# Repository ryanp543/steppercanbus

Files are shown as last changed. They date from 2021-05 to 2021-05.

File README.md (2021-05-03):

# CANBus Controlled Stepper Motor Driver 

## Overview

This repository contains the Autodesk Eagle schematic and layout for the custom stepper motor driver developed for the robotic arm mounted on the MIT Bioinstrumentation Lab rover. This information is found in the `Stepper CANBus V2` folder.

The driver had to be able to 1) fit in a CANBus network, 2) require the fewest numbers of wires to operate (in this case, power, ground, and the two CANBus lines), and 3) run on 21 V. What resulted from these constraints is a stepper driver that can be used universally with 24 V bipolar stepper motors and can be easily modified via the interface of the mounted Teensy. Despite the fact that the PCB shape is tailored to this robotic arm, multiple of these drivers can be linked together in any desired daisy chained CANBus network, as long as the last driver in the chain has the switch turned on to activate the 120 Ohm terminator resistor.

The microcontroller chosen for this driver was a Teensy 3.2 based on its widely used interface, easy customization, and relatively small size for a breakout board microcontroller. A Texas Instruments DRV8825 microstepper driver carrier board was selected so it could also be easily mounted onto the custom PCB and take commands from the Teensy. For the step-down power converter, a buck switching regulator (specifically Texas Instruments chip LM2594MX-5.0/NOPBCT-ND) was picked to provide a fixed 500 mA at 5 V, stepped down from an input voltage of around 20 to 24 V. External components such as capacitors and diodes were placed in the external circuit according to the data sheet.

The firmware that is uploaded to the Teensy from the Arduino IDE can be found in the `Stepper_CANBus_Firmware` directory. 

## Contributors

#### Primary Contributors
Ryan Poon from the [MIT Bioinstrumentation Lab](https://bioinstrumentation.mit.edu/) is the primary contributor of this project.

#### Other Contributors
Professor Ian Hunter served as the main advisor.

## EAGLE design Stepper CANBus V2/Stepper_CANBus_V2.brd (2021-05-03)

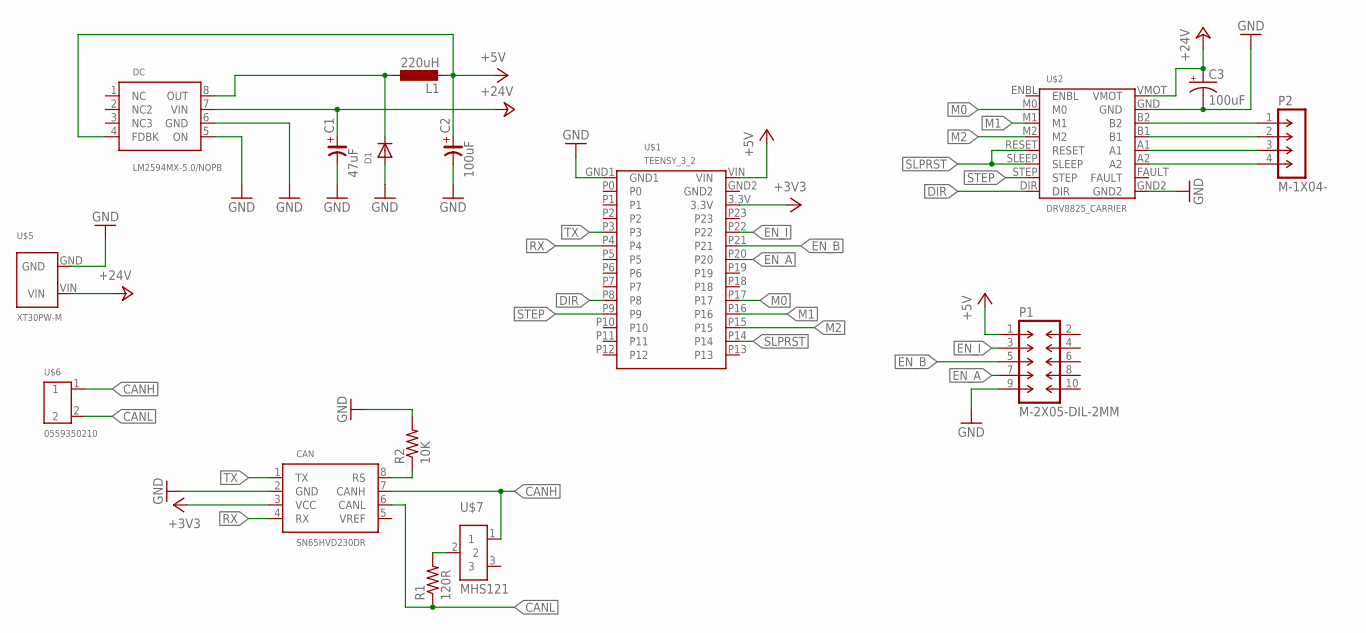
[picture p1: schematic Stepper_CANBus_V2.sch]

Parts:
C1: 47uF; C7343/T
C2: 100uF; C7343/T
C3: 100uF; E2,5-7
CAN: SN65HVD230DR; SOIC8
D1: DIODESOD-323F; SOD-323F
DC: LM2594MX-5.0/NOPB; SOIC8
L1: 220uH; L4532M
P1: M-2X05-DIL-2MM; DIL-2MM-2X05
P2: M-1X04-; DIL-2MM-1X04
R1: 120R; R0603
R2: 10K; R0603
U$1: TEENSY_3_2
U$2: DRV8825_CARRIER
U$5: XT30PW-M
U$6: 0559350210
U$7: MHS121

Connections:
+3V3: CAN.3 (VCC), U$1.3.3V
+5V: C2.+, DC.4 (FDBK), L1.2, P1.1, U$1.VIN
+24V: C1.+, C3.+, DC.7 (VIN), U$2.VMOT, U$5.VIN
CANH: CAN.7 (CANH), U$6.1, U$7.1
CANL: CAN.6 (CANL), R1.1, U$6.2
DIR: U$1.P8, U$2.DIR
EN_A: P1.7, U$1.P20
EN_B: P1.5, U$1.P21
EN_I: P1.3, U$1.P22
GND: C1.-, C2.-, C3.-, CAN.2 (GND), D1.A, DC.5 (ON), DC.6 (GND), P1.9, R2.2, U$1.GND1, U$2.GND, U$2.GND2, U$5.GND
M0: U$1.P17, U$2.M0
M1: U$1.P16, U$2.M1
M2: U$1.P15, U$2.M2
unnamed: CAN.8 (RS), R2.1
unnamed: D1.C, DC.8 (OUT), L1.1
unnamed: P2.1, U$2.B2
unnamed: R1.2, U$7.2
unnamed: P2.2, U$2.B1
unnamed: P2.3, U$2.A1
unnamed: P2.4, U$2.A2
RX: CAN.4 (RX), U$1.P4
SLPRST: U$1.P14, U$2.RESET, U$2.SLEEP
STEP: U$1.P9, U$2.STEP
TX: CAN.1 (TX), U$1.P3

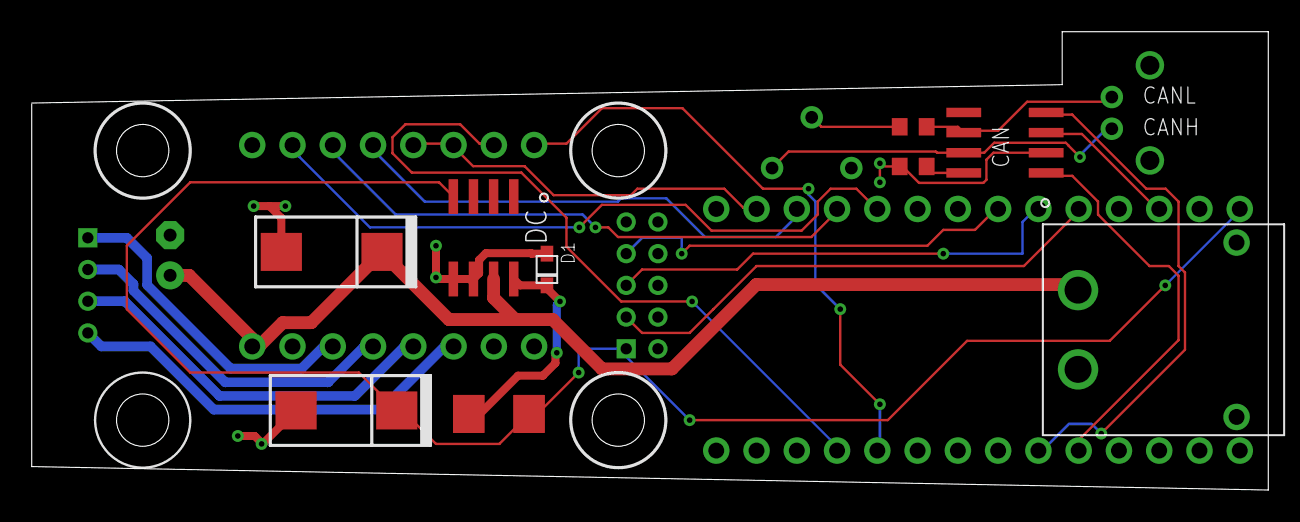
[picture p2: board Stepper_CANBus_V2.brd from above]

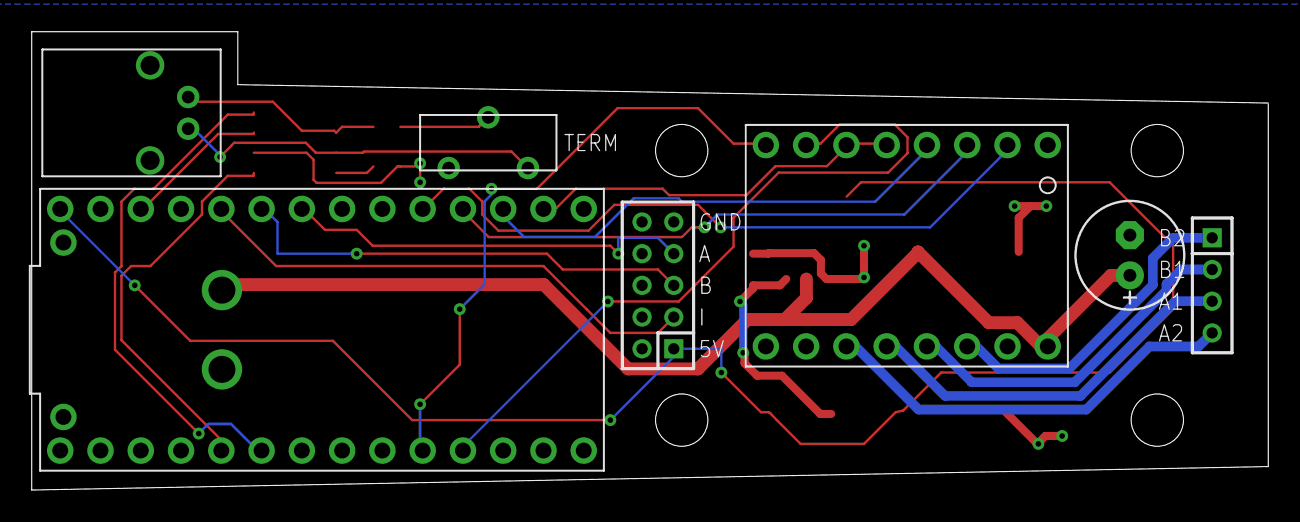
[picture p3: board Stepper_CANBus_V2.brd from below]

Board: 2 copper layers, 78.0 x 28.9 mm, 16 parts (7 on the bottom side), 24 nets.

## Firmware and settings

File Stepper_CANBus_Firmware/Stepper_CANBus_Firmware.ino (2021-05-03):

#include <AccelStepper.h>
#include <FlexCAN.h>

// Stepper constants
const float GEAR_RATIO = 25.2;
const float STEP_RESOLUTION = 200; // 200 steps per revolution
const float CURRENT = 1.5; // 1.5 amps current limit
const int MICROSTEP = 1;

// Encoder constants
const int COUNTS_PER_REV = 2000;
const int ENCODER_TYPE = 2; // X2 encoding

// CANBus ID and command unpacking constants;
const int8_t CAN_ID = 0x4;
const float P_MIN = -25.0f / 6.0f;
const float P_MAX = 25.0f / 6.0f;
const float V_MIN = -45.0f;
const float V_MAX = 45.0f;
const float KP_MIN = 0.0f;
const float KP_MAX = 500.0f;
const float KD_MIN = 0.0f;
const float KD_MAX = 5.0f;
const float T_MIN = -18.0f;
const float T_MAX = 18.0f;
const float I_MIN = -40.0f;
const float I_MAX = 40.0f;

// Initialize LED pin number
const int ledPin = 13;

// Initialize stepper motor pin numbers and variables
const int motorInterfaceType = 1;
const int M0 = 17;
const int M1 = 16;
const int M2 = 15;
const int dirPin = 8;
const int stepPin = 9;
const int sleepReset = 14;
float radPerSecond = 0.0;
volatile float oldPos = 0.0;
AccelStepper stepper = AccelStepper(motorInterfaceType, stepPin, dirPin);

// Initialize encoder pin numbers and variables 
bool atStart = false;
const int encoderA = 20;
const int encoderB = 21;
const int encoderI = 22;
volatile int encoderCount = 0;
volatile float actualPosition = 0.0;

// Initialize exampleClass and reception variable, which are used for CANbus reception. Also initialize transmission message
char reception[8];
char stored[8];
static CAN_message_t txmsg;

class ExampleClass : public CANListener {
public:
   void printFrame(CAN_message_t &frame, int mailbox);
   bool frameHandler(CAN_message_t &frame, int mailbox, uint8_t controller); //overrides the parent version so we can actually do something
};

bool ExampleClass::frameHandler(CAN_message_t &frame, int mailbox, uint8_t controller){
//   Serial.println((String)"ID: " + frame.id);
//   Serial.print("Data: ");
   for (int c = 0; c < frame.len; c++){
      reception[c] = frame.buf[c];
//      Serial.print(reception[c], HEX);
   }
//   Serial.write('\n');

   return true;
}

ExampleClass exampleClass;

void setup() {
  pinMode(ledPin, OUTPUT);

  // Pull sleepReset high
  pinMode(sleepReset, OUTPUT);
  digitalWrite(sleepReset, HIGH);

  // Setup stepper settings
  pinMode(dirPin, OUTPUT);
  pinMode(M0, OUTPUT);
  pinMode(M1, OUTPUT);
  pinMode(M2, OUTPUT);
  stepper.setMaxSpeed(10000);

  // Setup encoder settings
  pinMode(encoderA, INPUT);
  pinMode(encoderB, INPUT);
  pinMode(encoderI, INPUT);
  attachInterrupt(encoderA, doEncoderA, CHANGE);

  // Setup CANBus
  CAN_filter_t filter;
  filter.id = CAN_ID;
  filter.flags.extended = 0;
  filter.flags.remote = 0;
  Can0.begin(1000000);
  Can0.attachObj(&exampleClass);
  
  for (uint8_t filterNum=0; filterNum<8; filterNum++){
    Can0.setMask(0x7FF<<18, filterNum);
    Can0.setFilter(filter, filterNum);  
  }
  for (uint8_t filterNum=0; filterNum<8; filterNum++){
    exampleClass.attachMBHandler(filterNum);
  }

  // Setup Serial
  // Serial.begin(9600);
  // while (!Serial);

  // Setup microstep settings
  setSteps();
}

void loop() {
  digitalWrite(ledPin, HIGH);   // set the LED on
  // Serial.println("Waiting for CANBus entry");

  while (strlen(reception) < 8){
    delay(1);
  }
  memcpy(stored, reception, strlen(reception));
  memset(reception, 0, sizeof(reception));
  
  if (stored[0]==0xFF && stored[1]==0xFF && stored[2]==0xFF && stored[3]==0xFF && stored[4]==0xFF && stored[5]==0xFF && stored[6]==0xFF && stored[7]==0xFC){
    // Serial.println("Enabled motor"); 
    atStart = true;
  }
  else if (stored[0]==0xFF && stored[1]==0xFF && stored[2]==0xFF && stored[3]==0xFF && stored[4]==0xFF && stored[5]==0xFF && stored[6]==0xFF && stored[7]==0xFE){
    stepper.setCurrentPosition(0);
    if (atStart == true){
      // Serial.println("Zeroing motor at start");
      atStart = false;
      encoderCount = 0;
    }
    else{
      // Serial.println("Zeroing motor due to skipped steps");
      stepper.setCurrentPosition(calculateSteps(actualPosition));
    }
  }
  else{
    float* new_cmd = unpack_cmd(stored);
    radPerSecond = new_cmd[1];
    runStepper(new_cmd[0]); 

  }
  
}

// FUNCTIONS FOR MOVEMENT AND STEPPER SETTINGS

float calculateSteps(float rad){
  return (rad * (STEP_RESOLUTION/(2*PI)) * GEAR_RATIO * MICROSTEP);
}

float calculateRad(float steps){
  return ((2 * PI * steps) / (STEP_RESOLUTION * GEAR_RATIO * MICROSTEP));
}

void runStepper(float rad){
  float steps = calculateSteps(rad);
  float stepsPerSecond = calculateSteps(radPerSecond);
  if (steps < stepper.currentPosition()){
    stepsPerSecond = -1.0 * stepsPerSecond;
    radPerSecond = -1.0 * radPerSecond;
  }
  
  stepper.setSpeed(stepsPerSecond);

  if (stepper.currentPosition() < steps){
    while (stepper.currentPosition() <= steps){
//      Serial.print((String)"Expected position: ");
//      Serial.println(calculateRad(stepper.currentPosition()), 6);
//      Serial.println(actualPosition, 6);
      stepper.runSpeed();
      delay(1);
    }
  }
  else if (stepper.currentPosition() > steps){
    while (stepper.currentPosition() >= steps){
//      Serial.print((String)"Expected position: ");
//      Serial.println(calculateRad(stepper.currentPosition()), 6);
//      Serial.println(actualPosition, 6);
      stepper.runSpeed();
      delay(1);
    }
  }
  pack_reply(calculateRad(stepper.currentPosition()), radPerSecond);
//  pack_reply(actualPosition, radPerSecond); 
}

void setSteps(){  
  if (MICROSTEP < 16){
    digitalWrite(M2, LOW);
  }
  else{
    digitalWrite(M2, HIGH);
  }

  switch(MICROSTEP){
    case 1:
      digitalWrite(M0, LOW);
      digitalWrite(M1, LOW);
      Serial.println("FULL STEP | M0: LOW | M1: LOW | M2: LOW");
      break;
    case 2:
      digitalWrite(M0, HIGH);
      digitalWrite(M1, LOW);
      Serial.println("HALF STEP | M0: HIGH | M1: LOW | M2: LOW");
      break;
    case 4:
      digitalWrite(M0, LOW);
      digitalWrite(M1, HIGH);
      Serial.println("1/4 STEP | M0: LOW | M1: HIGH | M2: LOW");
      break;
    case 8:
      digitalWrite(M0, HIGH);
      digitalWrite(M1, HIGH);
      Serial.println("1/8 STEP | M0: HIGH | M1: HIGH | M2: LOW");
      break;
    case 16:
      digitalWrite(M0, LOW);
      digitalWrite(M1, LOW);
      Serial.println("1/16 STEP | M0: LOW | M1: LOW | M2: HIGH");
      break;
    case 32:
      digitalWrite(M0, HIGH);
      digitalWrite(M1, HIGH);
      Serial.println("1/32 STEP | M0: HIGH | M1: HIGH | M2: HIGH");
      break;
    default:
      Serial.println("MICROSTEP VALUE NOT VALID, PLEASE CHANGE");
      break;
  }
}

// FUNCTION INTERRUPTS FOR ENCODER 

void doEncoderA() {
  // look for a low-to-high on channel A
  if (digitalRead(encoderA) == HIGH) {
    // check channel B to see which way encoder is turning
    if (digitalRead(encoderB) == LOW) {
      encoderCount = encoderCount + 1;         // CW
    }
    else {
      encoderCount = encoderCount - 1;         // CCW
    }
  }
  // must be a high-to-low edge on channel A
  else {
    // check channel B to see which way encoder is turning
    if (digitalRead(encoderB) == HIGH) {
      encoderCount = encoderCount + 1;          // CW
    }
    else {
      encoderCount = encoderCount - 1;          // CCW
    }
  }
  actualPosition = (encoderCount * 2 * PI) / (COUNTS_PER_REV * GEAR_RATIO * ENCODER_TYPE);
  if ((encoderCount % 250) == 0){
      pack_reply(calculateRad(stepper.currentPosition()), radPerSecond);
      // Serial.println(actualPosition);
//    pack_reply(actualPosition, radPerSecond);
  }
}

// FUNCTIONS FOR CANBUS UNPACKING AND PACKING COMMANDS
float uint_to_float(int x_int, float x_min, float x_max, int bitNum){
  /// converts unsigned int to float, given range and number of bits ///
  float span = x_max - x_min;
  float off_set = x_min;
  return ((float)x_int)*span/((float)((1<<bitNum)-1)) + off_set;
}

int float_to_uint(float x, float x_min, float x_max, int bitNum){
  /// Converts a float to an unsigned int, given range and number of bits ///
  float span = x_max - x_min;
  float off_set = x_min;
  return (int) ((x-off_set)*((float)((1<<bitNum)-1))/span);
}

float* unpack_cmd(char *msg){
  float* cmd = new float[5];
  
  int p_int = (msg[0]<<8)|msg[1];
  int v_int = (msg[2]<<4)|(msg[3]>>4);
  int kp_int = ((msg[3]&0xF)<<8)|msg[4];
  int kd_int = (msg[5]<<4)|(msg[6]>>4);
  int t_int = ((msg[6]&0xF)<<8)|msg[7];

  // Serial.println(v_int);

  cmd[0] = uint_to_float(p_int, P_MIN, P_MAX, 16); // Negative for Gazebo purposes
  cmd[1] = uint_to_float(v_int, V_MIN, V_MAX, 12);
  cmd[2] = uint_to_float(kp_int, KP_MIN, KP_MAX, 12);
  cmd[3] = uint_to_float(kd_int, KD_MIN, KD_MAX, 12);
  cmd[4] = uint_to_float(t_int, T_MIN, T_MAX, 12);
  
  return cmd;
}

void pack_reply(float pos, float vel){
  pos = pos;
  vel = vel; 
  int p_int = float_to_uint(pos, P_MIN, P_MAX, 16);
  int v_int = float_to_uint(vel, V_MIN, V_MAX, 12);
  int t_int = float_to_uint(CURRENT, -T_MAX, T_MAX, 12);
  // Serial.println(p_int);
  // Serial.println(v_int);

  txmsg.id = 0x0;
  txmsg.len = 6;
    
  txmsg.buf[0] = CAN_ID;
  txmsg.buf[1] = p_int>>8;
  txmsg.buf[2] = p_int&0xFF;
  txmsg.buf[3] = v_int>>4;
  txmsg.buf[4] = ((v_int&0xF)<<4) + (t_int>>8);
  txmsg.buf[5] = t_int&0xFF;

  // for (int k=0; k<txmsg.len; k++){
  //  Serial.println(txmsg.buf[k]);
  // }

  Can0.write(txmsg);
}

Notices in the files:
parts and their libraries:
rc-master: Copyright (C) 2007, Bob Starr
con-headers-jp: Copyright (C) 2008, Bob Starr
